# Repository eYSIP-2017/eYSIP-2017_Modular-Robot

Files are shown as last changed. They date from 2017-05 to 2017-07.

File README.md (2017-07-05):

# eYSIP-2017_Modular-Robot
A modular robot largely based of Alberto's [Dtto:Modular Robot](https://hackaday.io/project/9976-dtto-explorer-modular-robot), with modifications to expand its sensing and autonomous decision making capabilities. 
## Project Log
* ### Week 1: 23/05/2017 to 28/05/2017
     - Did some research on existing Modular Robots and planned our approach.
     - Added report on project approach. Resources can be found here: https://goo.gl/4ZXmfM
     - Tested the components given: Servo SG90, Bluetooth Module HC05, Arduino Nano, 1s 500mAh LiPos and Sharp IR GP2Y0A21.
     - Added Wiki page 'Testing the modules involved'
     - Started learning V-Rep and Lua scripting for simulating robot motions. 
* ### Week 2: 29/05/2017 to 4/06/2017
     - Tested the VL53L0X Lased Distance Measurement sensor, which offers precise distance measurement in a tiny package.
     - Learned Lua scripting for V-REP simulations and also practiced on the V-REP environment to learn basics of it.
     - Detected Wall/Obstacle using proximity sensor and restructured modules to cross it using 4 modules snake in V-REP.
     - Added Wiki page 'V-REP Simulations'
     - Edited CAD files of modules to increase hole diameter to 2mm due to screw unavailability
     - *NOTE: Module development delayed due to screw unavailability and also lately facing problems in 3D printer*
* ### Week 3: 05/06/2017 to 11/06/2017
     - Progress presentation 1 given on 06/06/2017.
     - Interfaced RF Module NRF24L01 and servo MG90S(for the hinges).
     - First Dtto V2 module build completed! Tested crawl motion with existing program.
     - 1.5x4mm screws found, decreased hole diameter for future modules.
     - Started writing program from scratch.
* ### Week 4: 12/06/2017 to 18/06/2017
     - Dtto modules 2 and 3 completed!
     - Interfaced the VL53L0X ToF sensor on one of the female faces.
     - Robot halts when it detects and obstacle and continues when obstacle is removed
     - Concluded that motor torque of MG90S is insufficient for most transformations.
* ### Week 5: 19/06/2017 to 25/06/2017   
     - Progress demonstration on 20/06/2017
     - Added Wiki page 'Building the modules', updated previous pages with more content.
     - Uploaded Arduino code with documentation
     - Edited CAD files and printed few parts for 'Mega Dtto', a scaled up version in order to support high torque servo GOTECK GS-5515MG
     - Started exploring methods to create a virtual Dtto environment for directly programming transformations, and also as a test bench.
* ### Week 6: 25/06/2017 to 02/07/2017 
     - Module 4 completed!
     - Implemented wheel motion using 4 modules.
     - Completed Virtual Dtto for setting angles, snake motion using Python remoteApi in V-REP.
     - Created poster for project exhibition.
     - Project Exhibition on 30/06/2017
* ### Week 7: 03/07/2017 to 05/07/2017 
     - Code updated and with better documentation.
     - Created Wiki page 'Wheel Motion: 4 modules' and 'Virtual Dtto'.
     - Created Final Report for project submission.
     - Did some basic testing for the Mega Dtto module.

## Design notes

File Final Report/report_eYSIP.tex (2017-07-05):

\documentclass[a4paper,12pt,oneside]{book}

%-------------------------------Start of the Preable------------------------------------------------
\usepackage[english]{babel}
\usepackage{blindtext}
%packagr for hyperlinks
\usepackage{hyperref}
\hypersetup{
    colorlinks=true,
    linkcolor=blue,
    filecolor=magenta,      
    urlcolor=cyan,
}

\urlstyle{same}
%use of package fancy header
\usepackage{fancyhdr}
\setlength\headheight{26pt}
\fancyhf{}
%\rhead{\includegraphics[width=1cm]{logo}}
\lhead{\rightmark}
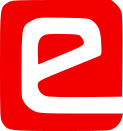
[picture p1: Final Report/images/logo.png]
\rhead{}
\fancyfoot[RE, RO]{\thepage}
\fancyfoot[CE, CO]{\href{http://www.e-yantra.org}{www.e-yantra.org}}

\pagestyle{fancy}

%use of package for section title formatting
\usepackage{titlesec}
\titleformat{\chapter}
  {\Large\bfseries} % format
  {}                % label
  {0pt}             % sep
  {\huge}           % before-code
 
%use of package tcolorbox for colorful textbox
\usepackage[most]{tcolorbox}
\tcbset{colback=cyan!5!white,colframe=cyan!75!black,halign title = flush center}

\newtcolorbox{mybox}[1]{colback=cyan!5!white,
colframe=cyan!75!black,fonttitle=\bfseries,
title=\textbf{\Large{#1}}}

%use of package marginnote for notes in margin
\usepackage{marginnote}

%use of packgage watermark for pages
%\usepackage{draftwatermark}
%\SetWatermarkText{\includegraphics{logo}}
\usepackage[scale=2,opacity=0.1,angle=0]{background}
\backgroundsetup{
contents={}
}

%use of newcommand for keywords color
\usepackage{xcolor}
\newcommand{\keyword}[1]{\textcolor{red}{\textbf{#1}}}

%package for inserting pictures
\usepackage{graphicx}
\graphicspath{ {images/} }

%package for highlighting
\usepackage{color,soul}

\usepackage{tikz}

\newcommand{\ExternalLink}{%
    \tikz[x=1.2ex, y=1.2ex, baseline=-0.05ex]{% 
        \begin{scope}[x=1ex, y=1ex]
            \clip (-0.1,-0.1) 
                --++ (-0, 1.2) 
                --++ (0.6, 0) 
                --++ (0, -0.6) 
                --++ (0.6, 0) 
                --++ (0, -1);
            \path[draw, 
                line width = 0.5, 
                rounded corners=0.5] 
                (0,0) rectangle (1,1);
        \end{scope}
        \path[draw, line width = 0.5] (0.5, 0.5) 
            -- (1, 1);
        \path[draw, line width = 0.5] (0.6, 1) 
            -- (1, 1) -- (1, 0.6);
        }
    }

%new command for table
\newcommand{\head}[1]{\textnormal{\textbf{#1}}}

%----------------------End of the Preamble---------------------------------------

\begin{document}

%---------------------Title Page------------------------------------------------
\begin{titlepage}
\raggedright
{\Large eYSIP 2017\\[1cm]}
{\Huge\scshape Modular Robot \\[.1in]}
\vfill
\begin{flushright}
{\large Srijal Poojari \\}
{\large Madhav Wagh \\}
{\large Mentors: Pushkar Raj, Aditya Panwar and Fayyaz Pocker \\}
{\large Duration of Internship: $ 22/05/2017-07/07/2017 $ \\}
\end{flushright}

{\itshape 2017, e-Yantra Publication}
\end{titlepage}
%-------------------------------------------------------------------------------

\chapter[Project Tag]{Modular Robot}
\section*{Abstract}
  This project is about homogeneous modular robotic modules, 
  which are coupled using mechanical and magnetic coupling. 
  The goal of the project is to explore existing modular robots, mainly the Dtto: Modular robot and expanding its capabilities. \\
  The modules are initially tested in a simulation environment for their feasibility (V-REP) and sensors (ToF) are interfaced to the modules for smart sensing and decision making. Snake motion, wheel motion, coupling/decoupling, obstacle detection and avoidance are achieved in practice. 

\subsection*{Completion status}
\textbf{Tasks given: }
\begin{enumerate}
\item Getting familiar with existing Models of Modular Robots\\ Status: Completed
\\ Details: Report has been earlier submitted on existing Modular Robots and project approach.

\item Interfacing Arduino ide with Servo, Bluetooth and Sensor 
\\ Status: Completed
\\ Details: Interfacing was completed with the following: Sharp IR 2Y0A21, Servo motors, Bluetooth module HC-05, nRF24L01 radio module and VL53L0X LASER ToF sensor.

\item Testing and selecting appropriate sensors to be added in the module.
\\ Status: Completed
\\ Details: Sensors were interfaced and the Vl53L0X was added to one of the modules.

\pagebreak

\item Making design changes in the modules for accommodating sensors. Adding more degree of freedom to the robot
\\ Status: Partially Completed
\\ Details: Design changes were done for the available screw sizes. Increasing degree of freedom of the robot was not achieved/supported by the Dtto v2 modules.

\item Assembling all the selected parts. Four robotic modules need to be produced.
\\ Status: Completed
\\ Details: Four robotic modules have been produced.

\item Applying algorithm to check different types of motion. Example: Wheel, Ladder, Snake.
\\ Status: Partially Completed
\\ Details: Wheel and Snake motion has been implemented. Servo motors are not powerful enough for Ladder maneuver.

\item Autonomous obstacle avoidance using sensor detection and self- reconfiguration.
\\ Status: Partially Completed
\\ Details: Obstacle detection has been achieved but self-reconfiguration is restricted by insufficient torque from servo motors.

\item Code and Documentation
\\ Status: Completed
\\ Details: The complete documentation and code can be found on our \href{https://github.com/eYSIP-2017/eYSIP-2017_Modular-Robot}{GitHub repository}.

\end{enumerate}

\noindent \textbf{Other work:}

\begin{enumerate}
\item V-REP simulations were performed while we were having problems finding the right screws and servo motors for the hinges.

\item A 'mega' Dtto module has been produced with larger size using the GO TECK GS-5515MG servo motors at the hinges

\item 'Virtual Dtto' environment has been created in V-REP using the python remoteApi for accepting commands via Bluetooth from the user which gets reflected on the simulated model. 

\end{enumerate}

\pagebreak

\section{Hardware parts}
\begin{itemize}
\item Primary:
      \begin{enumerate}
          \item Arduino Nano
          \\The brain of the Dtto. The main program runs on this and controls all others components in the Dtto.

          \item Bluetooth Module (HC-05)
          \\The HC-05 in the master module pairs up with the user's smartphone/tablet to accept commands from the user.

          \item RF Module (nRF24L01)
          \\The received commands by master is broadcasted to the slave modules (whenever required), which is the primary commands for slave modules

          \item Servo Motors (MG90S, SG90)
          \\Servo motors drive the module hinges and hooking mechanism. There are 5 servos used in total per module(2xMG90S-for the hinges and 3xSG90-for the hooks).

          \item VL53LOX LASER ToF Sensor 
          \\This is used to measure the distance from the module's base face (at the right moment) to detect obstacles present while the modules move.

      \end{enumerate}
      
\item Secondary:
      \begin{enumerate}
          \item Power: 2x 1s, 500mAh LiPos in series is given to the Arduino Nano at the Vin pin directly, and is regulated to 5.8V using an LM317 variable voltage regulator for the servos.

          \item Neodymium magnets: 4mm diameter, 3mm height(or 2x1.5mm stacked) are used for alignment of hooking mechanism when male and female faces are brought together. \\
          Amount required per module: 24/48 pieces for 3/1.5mm height

          \item Resistors (2.2k, 1.2k, 330), connecting wires, latching switch, prototype perf board, male and female headers, rubber bands.

      \end{enumerate}
\end{itemize}

\pagebreak

\section{Software used}
\begin{itemize}
\item Arduino IDE \\
Used to create and upload 'sketches' to the Arduino Nano. Also has a handy Serial Monitor for debugging.
\\Version used: 1.8.2
\\Download Link: \href{https://www.arduino.cc/en/main/software}{https://www.arduino.cc/en/main/software} 

\item Sloeber Eclipse IDE for Arduino\\
This is an alternative to the Arduino IDE which enables us to program the Arduino using the feature rich Eclipse IDE for C/C++. Most of out Dtto sketch was written on this.
\\Version used: 4.1 Beryllium
\\Download Link: \href{http://www.baeyens.it/eclipse/}{http://www.baeyens.it/eclipse/} 

\item Coppelia Robotics V-REP Simulator\\
V-REP was used for simulating the Dtto and also to create the Virtual Dtto environment.
\\Version used: 3.4.0
\\Download Link: \href{http://www.coppeliarobotics.com/downloads.html}{http://www.coppeliarobotics.com/downloads.html} 

\item Autodesk Fusion 360 \\
Used to modify the 3D CAD files of the modules before 3D printing them.
\\Version used: 2.0.3034
\\Download Link: \href{https://www.autodesk.com/products/fusion-360/students-teachers-educators}{https://www.autodesk.com/products/fusion-360/students-teachers-educators} 

\item Python 2.7\\
Python is necessary to run the Virtual Dtto as we are using the Python remoteApi for V-REP.
\\Version used: 2.7.13
\\Download Link: \href{https://www.python.org/downloads/release/python-2713/}{https://www.python.org/downloads/release/python-2713/} 

\item Fritzing\\
Fritzing was used to create all the schematics and interfacing diagrams.
\\Version used: 0.9.3b
\\Download Link: \href{http://fritzing.org/download/}{http://fritzing.org/download/}

\end{itemize}

\pagebreak

\section{Assembly of hardware}

\subsection{Circuit Diagram}
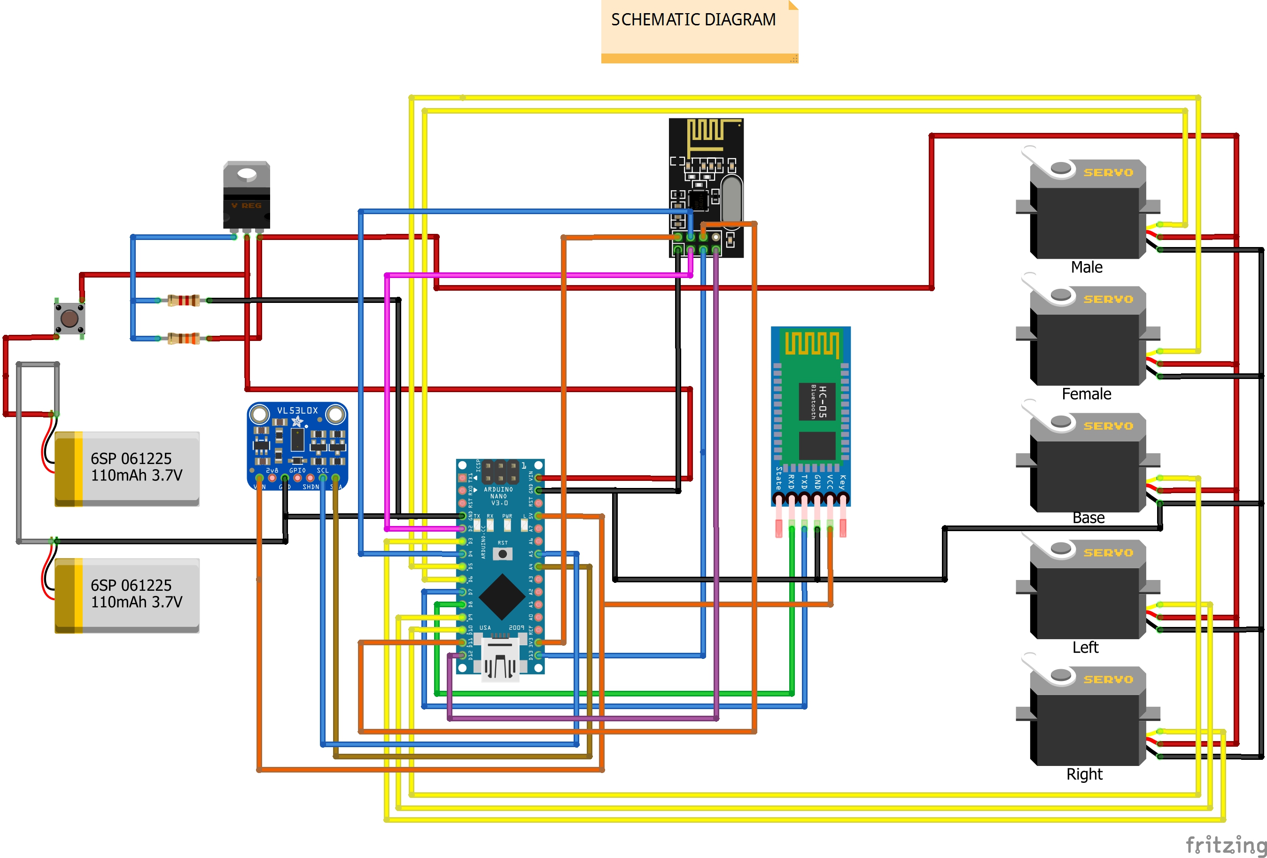
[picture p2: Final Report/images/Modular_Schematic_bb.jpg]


\subsection{Steps for assembly}
Steps for assembly can be found in this separate file \href{./Assembly steps for Dtto v2 Module.pdf}{here}.

\pagebreak

\section{Software and Code}

The program can be found in the eYSIP repository 
\href{https://github.com/eYSIP-2017/eYSIP-2017_Modular-Robot}{here}.\\

\noindent The entire program flow can be described by the flowcharts below:

\begin{itemize}

\item General flow \\
\begin{center}
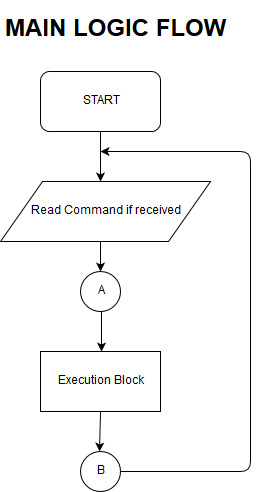
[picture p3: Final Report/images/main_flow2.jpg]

\end{center}

\end{itemize}
\pagebreak

\noindent The execution part can be elaborated further based on the type of command:

\begin{itemize}
\item Set angle \\

\vspace{-20pt}
\begin{center}
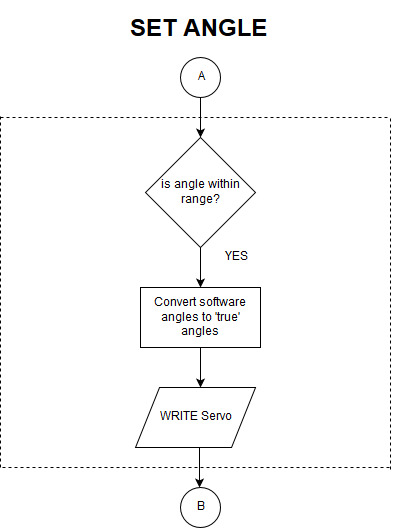
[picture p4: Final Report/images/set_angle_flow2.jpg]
 
\end{center}

\item Wheel \\
\vspace{-20pt}
\begin{center}
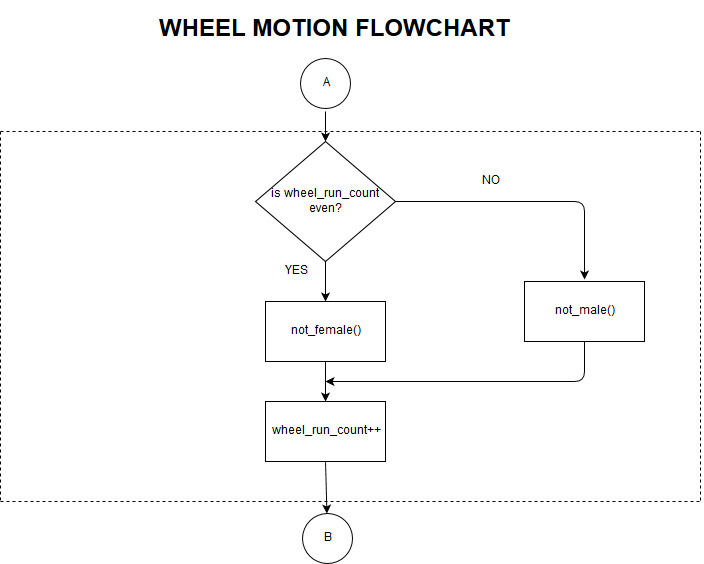
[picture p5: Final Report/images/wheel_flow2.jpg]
 
\end{center}

\item Snake \\
\begin{center}
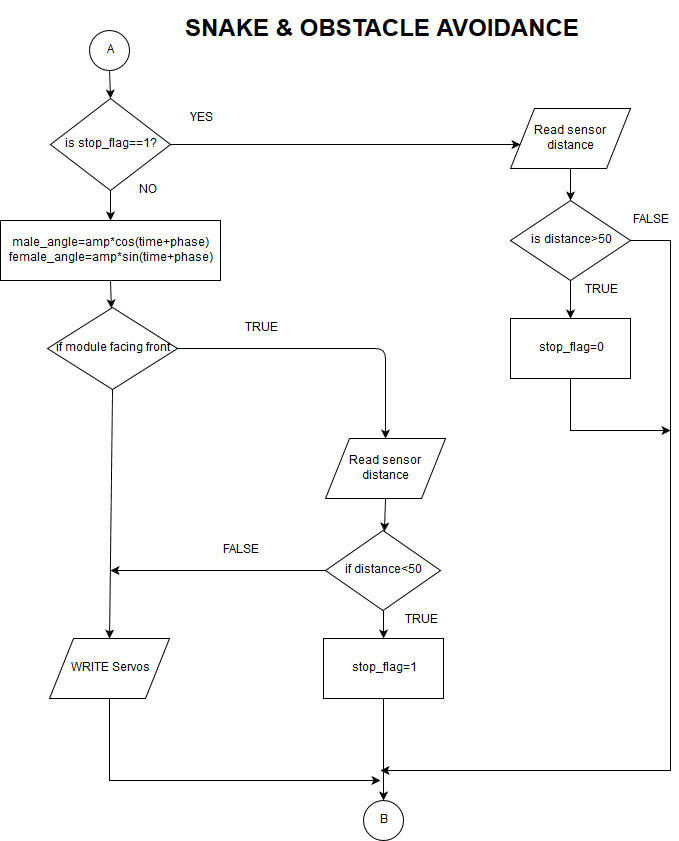
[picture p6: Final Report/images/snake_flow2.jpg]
 
\end{center}

\end{itemize}

\noindent Other than this, the entire code is well documented for detailed insights.

\pagebreak

\section{Use and Demo}
\subsection{Final Setup}
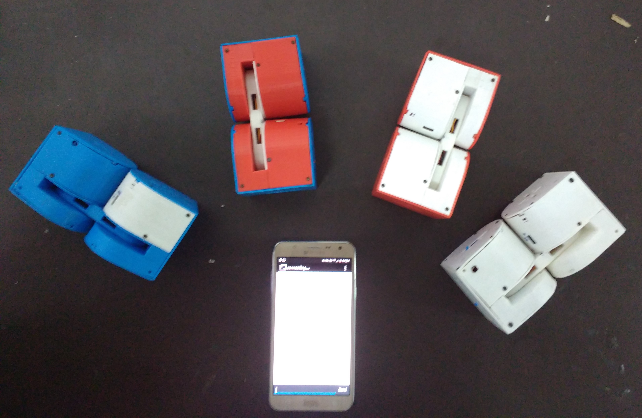
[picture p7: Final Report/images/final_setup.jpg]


\vspace{10pt}

\noindent The 4 Dtto modules assembled can be commanded using a Bluetooth device such as a smartphone shown above. The terminal application for Android devices can be downloaded \href{https://play.google.com/store/apps/details?id=Qwerty.BluetoothTerminal}{here}.

\subsection{User Instruction}
\noindent Load the Bluetooth Terminal application and connect to the master module from Options, Connect a device - Secure, 'Name of master HC-05'. Send the required commands. Best way to check all modules is by sending 'arm', which is to generate snake motion in all modules.

\vspace{10pt}

\noindent Structure of commands for controlling the Dtto using Bluetooth can be found in '\href{./Command_Definition.pdf}{Command\_Definitions.pdf}' present with this report or in our GitHub repository \href{https://github.com/eYSIP-2017/eYSIP-2017_Modular-Robot/blob/master/Final\%20Report/Command_Definition.pdf}{here}.

\subsection{Demonstration Video}
\begin{itemize}
\item \noindent Demonstration of snake motion and obstacle avoidance. \href{https://youtu.be/fWWrK-H1P5A}{\ExternalLink}

\item \noindent Demonstration of wheel motion. \href{https://youtu.be/WYdw9-lhOyw}{\ExternalLink}
\end{itemize}

\pagebreak

\section{Future Work}
There is vast amount of research and work which can be done
in the field of modular robotics and in our project, some 
enhancements which can be implemented in future are:

\begin{enumerate}
\item For faster processing and space saving, ESP8266/ESP32 can be used in place of Arduino Nano.

\item Using the basic modules implemented in the project with an overhead camera which can provide a reference frame for all modules.

\item Increasing the DOF of each module by adding rotating faces like the Dtto v3 which is under works.

\item Adding additional sensors for more feedback such as a  gravity sensor which can act as a reference for hinge angles.

\item Using a higher torque motor on the 'mega' modules being developed can add possibilities of different motions and transformations.
\end{enumerate}

\section{Bug report and Challenges}
\begin{itemize}
\item Appropriate screws (M1.7 x 4mm Flathead) were unavailable, so the CAD design was modified multiple times and the printing and assembly of modules was delayed.

\item The specified servo motor, MG92B is unavailable in local and online stores in India, so we're forced to use a lower torque motor MG90S, which is the closest that can be fit under the given module dimensions. Because of this many of the transformations was not possible.
\end{itemize}

\begin{thebibliography}{li}

\bibitem{dtto_alberto}
Alberto,
{\em Dtto - Explorer Modular Robot},
2016. \href{https://hackaday.io/project/9976-dtto-explorer-modular-robot}{\ExternalLink}

\bibitem{vrep_manual} 
V-REP User Manual. \href{http://www.coppeliarobotics.com/helpFiles/}{\ExternalLink}

\bibitem{hc05}
HC-05 specifications and AT commands. \href{https://www.itead.cc/wiki/Serial_Port_Bluetooth_Module_(Master/Slave)_:_HC-05}{\ExternalLink}

\bibitem{servo_cad}
Servo SG90, 3D CAD model. \href{https://grabcad.com/library/tower-pro-sg92r-servo-motor-1}{\ExternalLink}

\end{thebibliography}

\end{document}

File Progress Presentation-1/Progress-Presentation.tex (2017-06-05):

\documentclass[10pt, a4paper]{beamer}

\usetheme{Berkeley}
\usecolortheme{sidebartab}

\usepackage{graphicx}
\graphicspath{ {images/} }

\begin{document}
	\setbeamertemplate{sidebar left}{}
	\title{Progress Presentation-I}
	\subtitle{e-Yantra Summer Intership-2017 \\ Modular Robots}
	\author{Srijal Poojari\\Madhav Wagh\\
	\textbf{Mentors}: \\
	 Pushkar Raj, Aditya Panwar and Fayyaz Pocker}
	\institute{IIT, Bombay}
	\date{\today}
	%\addtobeamertemplate{sidebar left}{}{\includegraphics[scale = 0.3]{logowithtext.png}}
	\frame{\titlepage}

\setbeamertemplate{sidebar left}[sidebar theme]
\section{Overview of Project}
\begin{frame}{Overview of Project}
	\begin{itemize}
		\item \textbf{Project Name}:  Modular Robots
		\item \textbf{Objective} 
		\begin{enumerate}
		\item To build a Self-reconfigurable autonomous 	     		robot which can deliberately change shape by 				reorganizing connectivity between the modules.
		\linebreak
		\item To add sensors to the robot and make it smart. 		\\(To sense and take action according to the 				  environment)
		\linebreak
		\end{enumerate}
		\item \textbf{Deliverables}
		\begin{enumerate}
		 \item A stable modular robot which is able to 					  change its shape upon the need of the 					  environment.\linebreak
		\item Code and Documentation of each Task.
		\end{enumerate}
	\end{itemize}
\end{frame}

\section{Overview of Task}
\begin{frame}{Overview of Task}
	\begin{center}
    \begin{tabular}{ | l | p{6cm} | l |}
    \hline
     \textbf{Task No.} & \textbf{Task} & \textbf{Deadline}\\ \hline
     1 & Getting Familiar with existing models of Modular Robots & 2 days  \\ \hline
     
     2 & Interfacing Arduino IDE with Servo, Bluetooth and Sensor & 3 days  \\ \hline
     
     3 & Testing and selecting appropriate sensors to be added in the module & 2 days  \\ \hline
     
     4 & Make design changes in the modules for accommodating sensors.  & 4 days  \\ \hline
      
     5 & Assembling all the selected parts. Four robotic modules need to be produced & 4 days  \\ \hline
     
     6 & Applying algorithm to check different types of motion (Wheel, Snake, Ladder)  & 7 days  \\ \hline
     
     7 & Autonomous Obstacle Avoidance using sensor detection and self-reconfiguration & 6 days  \\ \hline
     
     8 & Code \& Documentation & 6 days  \\ \hline

    \end{tabular}
\end{center}
	
\end{frame}

\section{Tasks Accomplised}
\begin{frame}{Tasks Accomplised}
	\begin{itemize}
		\item \textbf{Task-1: Getting familiar with existing Modular Robots.}
		  \begin{itemize}
		  \item Collected information on existing modular robots.
		  \item Prepared a report and concluded that the Dtto Modular Robot is the most promising option under the given time and resources.
           \end{itemize}
           \vspace{15pt}
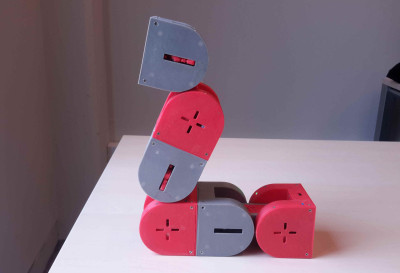
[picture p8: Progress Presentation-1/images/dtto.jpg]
        \centering   
		
	\end{itemize}
\end{frame}

\section{Tasks Accomplised}
\begin{frame}{Tasks Accomplised}
	\begin{itemize}
\item \textbf{Task-2 + 3: Selecting and interfacing sensors, servo motor and Bluetooth module with an Arduino.}
		\begin{itemize}
		  \item Successfully interfaced Bluetooth module HC-05 to HC-05 and HC-05 to PC/Android communication.
		  \item Interfaced servo motors and tested the Sharp IR sensor and VL53L0X ToF sensor for obstacle detection/distance measurement.
           \end{itemize}
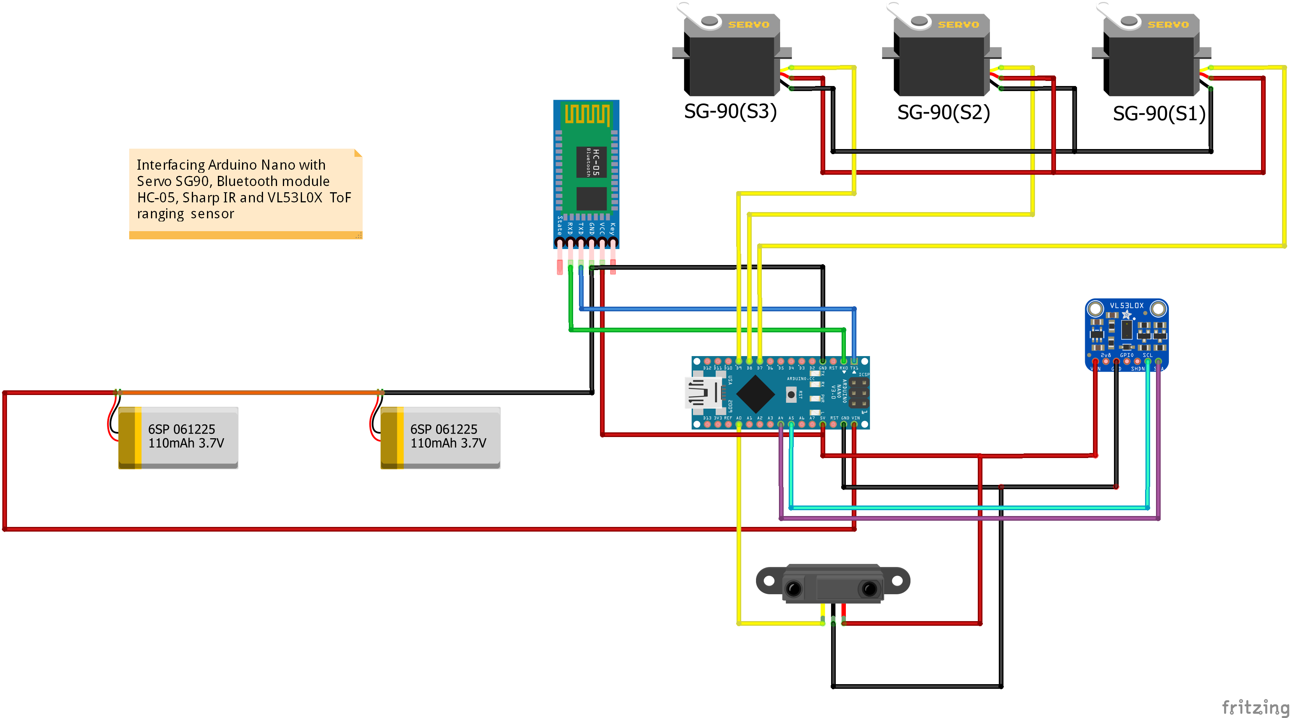
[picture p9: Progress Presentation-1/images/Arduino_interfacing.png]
           \centering
	\end{itemize}
\end{frame}

\section{Tasks Accomplised}
\begin{frame}{Tasks Accomplised}
	\begin{itemize}
		\item \textbf{Task-4: Making design changes in the modules.}
		\begin{itemize}
		    \item No major design changes were required as the modules have space for the tiny VL53L0X distance measurement sensor. 
		    \item Holes for the screws had to be expanded due to unavailability of M1.7x4mm screws.
		\end{itemize}
		\vspace{15pt}
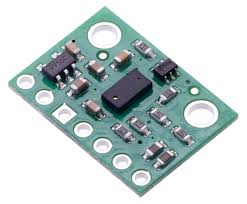
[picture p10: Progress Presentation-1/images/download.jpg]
        \centering
	\end{itemize}
\end{frame}

\section{Tasks Accomplised}
\begin{frame}{Tasks Accomplised}
	\begin{itemize}
		\item \textbf{Simulations in V-REP}
		    \begin{itemize}
		    \item Got familiar with the V-REP environment with Lua scripting and implemented practice simulations.
		    \item Understood existing Dtto movements and modified design to add proximity sensor which can detect obstacles and also measure its height.
		    \item Crossed the detected obstacles by reshaping modules in V-REP. \\ See video.
             \end{itemize}
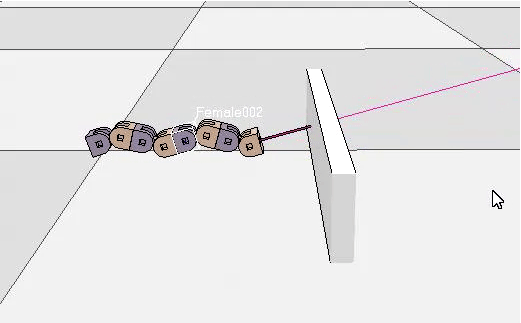
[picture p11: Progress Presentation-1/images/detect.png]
             \centering
	\end{itemize}
\end{frame}

\section{Tasks Accomplised}
\begin{frame}{Tasks Accomplised}
\begin{itemize}
		\item \textbf{Code and Documentation}
		    \begin{itemize}
		    \item Uploaded well-commented code (Arduino + Simulations) on GitHub for every stage.
		    \item Maintaining a detailed documentation of every step we take on GitHub Wiki of our repository.
            \end{itemize}
            
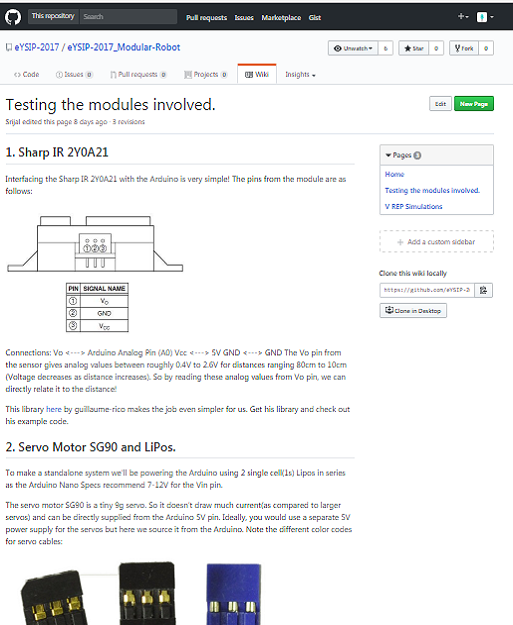
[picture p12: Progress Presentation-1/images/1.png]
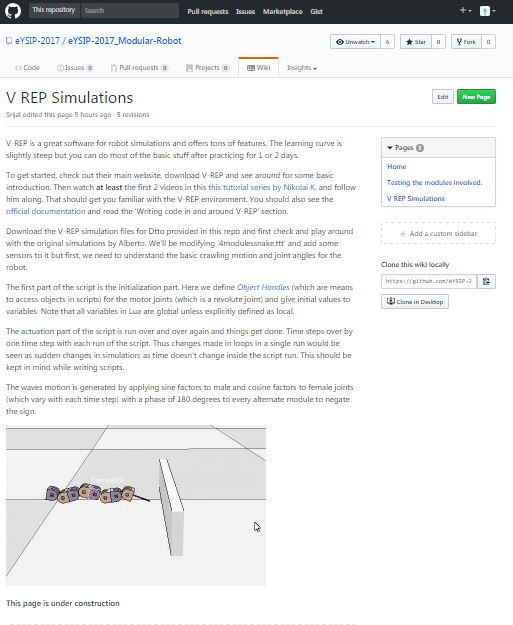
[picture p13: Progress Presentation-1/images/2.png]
        
            
\end{itemize}
\end{frame}		

\section{Challenges Faced}
\begin{frame}{Challenges Faced}
	\begin{itemize}
		\item Appropriate screws (M1.7x4mm Flathead) were unavailable, so the CAD design was modified multiple times and the printing and assembling of modules has been delayed. \linebreak
		\item The specified Servo motor, MG92B is unavailable in local and online stores so we're forced to use a lower torque motor MG90S, which is the closest that can be fit under the given module dimensions.
 
	\end{itemize}
\end{frame}

\section{Future Plans}
\begin{frame}{Future Plans}
	\begin{itemize}
		\item All printed parts assembled. Four Robotic modules to be assembled.
		
		\item Develop effective and generalized algorithms for different motions.
		
		\item  Obstacle detection using sensors and decision making to avoid/overcome the obstacle while robot moves from one point to another.

	\end{itemize}
\end{frame}

\section{Thank You}
\begin{frame}{Thank You}
	\centering\LARGE Thank You !
\end{frame}
\end{document}

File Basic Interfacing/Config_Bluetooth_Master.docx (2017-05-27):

STEPS TO CONFIGURE BLUETOOTH AS MASTER USING FTDI232

STEP-1) Interface the Bluetooth Module with the FT232 (USB to Serial Converter) as shown in Config_Bluetooth_ATComm.

STEP-2) Connect the FT232 to the USB Port of PC

After Connecting there will be a constant (POWER LED) on FT232 and a LED blinking quickly (twice in 1 second) on HC05.

STEP-3) If, FT232 driver software not installed, install it from (http://www.ftdichip.com/FTDrivers.htm)

STEP-4) Open the Serial Port on which FT232 driver is connected.

STEP-5) Master Configuration

1) Send AT Command. (Before Pressing Enter Press the Small button above EN Pin on HC05 (for AT Mode))

Get a Reply as OK

2) SEND AT+ROLE?

Will get a reply as 0 or 1, 0=> Slave, 1=> Master

3) SEND AT+ROLE=1 (Setting Module as Master)

4) SEND AT+NAME=MASTER-HC-05 (Renaming the Module)

5) SEND AT+NAME? (Checking Name of the Module)

6) SEND AT+CMODE=1 (Allows connecting to any address, Default CMODE is 0)

7) To bind another slave you need to bind with its MAC Address (48 bit address)

SEND AT+BIND= 0124, 71, CE187D

(Binding to the Slave module having MAC Address 01:24:71: CE: 18:7D)

8) SEND AT+BIND?

(Check all the Slave Bluetooth modules bound with the master)

Will return the MAC Address of modules which are bound

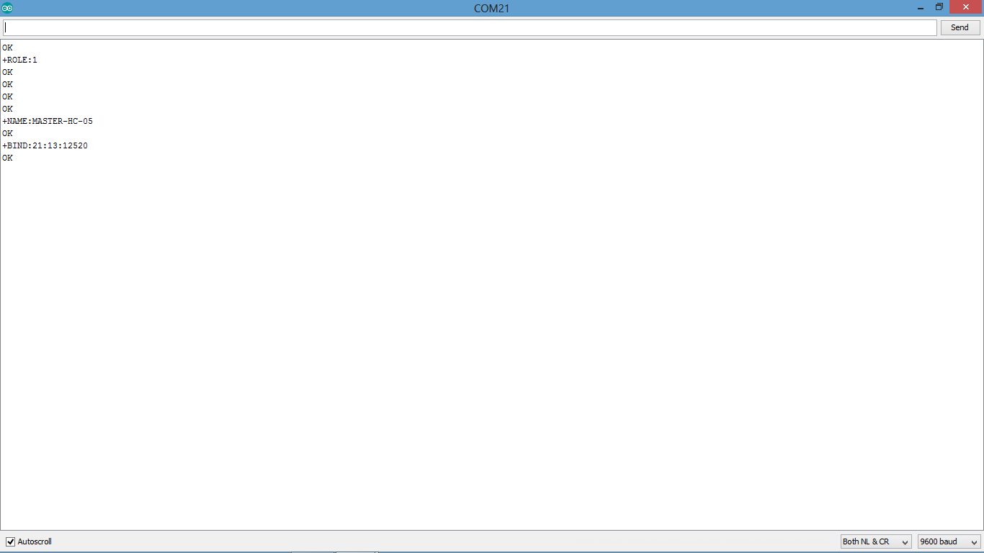
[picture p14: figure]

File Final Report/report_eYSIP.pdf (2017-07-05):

## eYSIP 2017

### Modular Robot

### Srijal Poojari Madhav Wagh Mentors: Pushkar Raj, Aditya Panwar and Fayyaz Pocker Duration of Internship: 22/05/2017 − 07/07/2017

2017, e-Yantra Publication

# Modular Robot

## Abstract

This project is about homogeneous modular robotic modules, which are coupled using mechanical and magnetic coupling. The goal of the project is to explore existing modular robots, mainly the Dtto: Modular robot and expanding its capabilities.
The modules are initially tested in a simulation environment for their feasibility (V-REP) and sensors (ToF) are interfaced to the modules for smart sensing and decision making. Snake motion, wheel motion, coupling/decoupling, obstacle detection and avoidance are achieved in practice.

### Completion status

Tasks given:

1. Getting familiar with existing Models of Modular Robots
Status: Completed
Details: Report has been earlier submitted on existing Modular Robots and project approach.
2. Interfacing Arduino ide with Servo, Bluetooth and Sensor
Status: Completed
Details: Interfacing was completed with the following: Sharp IR 2Y0A21, Servo motors, Bluetooth module HC-05, nRF24L01 radio module and VL53L0X LASER ToF sensor.
3. Testing and selecting appropriate sensors to be added in the module. Status: Completed
Details: Sensors were interfaced and the Vl53L0X was added to one of the modules.

1

4. Making design changes in the modules for accommodating sensors. Adding more degree of freedom to the robot
Status: Partially Completed
Details: Design changes were done for the available screw sizes. Increasing degree of freedom of the robot was not achieved/supported by the Dtto v2 modules.
5. Assembling all the selected parts. Four robotic modules need to be produced.
Status: Completed
Details: Four robotic modules have been produced.
6. Applying algorithm to check different types of motion. Example: Wheel, Ladder, Snake.
Status: Partially Completed
Details: Wheel and Snake motion has been implemented. Servo motors are not powerful enough for Ladder maneuver.
7. Autonomous obstacle avoidance using sensor detection and self- reconfiguration.
Status: Partially Completed
Details: Obstacle detection has been achieved but self-reconfiguration is restricted by insufficient torque from servo motors.
8. Code and Documentation
Status: Completed
Details: The complete documentation and code can be found on our GitHub repository. (https://github.com/eYSIP-2017/eYSIP-2017_Modular-Robot)

Other work:

1. V-REP simulations were performed while we were having problems finding the right screws and servo motors for the hinges.
2. A ’mega’ Dtto module has been produced with larger size using the GO TECK GS-5515MG servo motors at the hinges
3. ’Virtual Dtto’ environment has been created in V-REP using the python remoteApi for accepting commands via Bluetooth from the user which gets reflected on the simulated model.
www.e-yantra.org | 2

1.1. HARDWARE PARTS

## 1.1 Hardware parts

- Primary:
1. Arduino Nano
The brain of the Dtto. The main program runs on this and controls all others components in the Dtto.
2. Bluetooth Module (HC-05)
The HC-05 in the master module pairs up with the user’s smartphone/tablet to accept commands from the user.
3. RF Module (nRF24L01)
The received commands by master is broadcasted to the slave modules (whenever required), which is the primary commands for slave modules
4. Servo Motors (MG90S, SG90)
Servo motors drive the module hinges and hooking mechanism. There are 5 servos used in total per module(2xMG90S-for the hinges and 3xSG90-for the hooks).
5. VL53LOX LASER ToF Sensor
This is used to measure the distance from the module’s base face (at the right moment) to detect obstacles present while the modules move.
- Secondary:
1. Power: 2x 1s, 500mAh LiPos in series is given to the Arduino Nano at the Vin pin directly, and is regulated to 5.8V using an LM317 variable voltage regulator for the servos.
2. Neodymium magnets: 4mm diameter, 3mm height(or 2x1.5mm stacked) are used for alignment of hooking mechanism when male and female faces are brought together.
Amount required per module: 24/48 pieces for 3/1.5mm height
3. Resistors (2.2k, 1.2k, 330), connecting wires, latching switch, prototype perf board, male and female headers, rubber bands.
www.e-yantra.org | 3

1.2. SOFTWARE USED

## 1.2 Software used

- Arduino IDE
Used to create and upload ’sketches’ to the Arduino Nano. Also has a handy Serial Monitor for debugging.
Version used: 1.8.2
Download Link: https://www.arduino.cc/en/main/software
- Sloeber Eclipse IDE for Arduino
This is an alternative to the Arduino IDE which enables us to program the Arduino using the feature rich Eclipse IDE for C/C++. Most of out Dtto sketch was written on this.
Version used: 4.1 Beryllium
Download Link: http://www.baeyens.it/eclipse/
- Coppelia Robotics V-REP Simulator
V-REP was used for simulating the Dtto and also to create the Virtual Dtto environment.
Version used: 3.4.0
Download Link: http://www.coppeliarobotics.com/downloads.html
- Autodesk Fusion 360
Used to modify the 3D CAD files of the modules before 3D printing them.
Version used: 2.0.3034
Download Link: https://www.autodesk.com/products/fusion-360/studentsteachers-educators (https://www.autodesk.com/products/fusion-360/students-teachers-educators)
- Python 2.7
Python is necessary to run the Virtual Dtto as we are using the Python remoteApi for V-REP.
Version used: 2.7.13
Download Link: https://www.python.org/downloads/release/python-2713/ (https://www.python.org/downloads/release/python-2713/)
- Fritzing
Fritzing was used to create all the schematics and interfacing diagrams. Version used: 0.9.3b
Download Link: http://fritzing.org/download/
www.e-yantra.org | 4

1.3. ASSEMBLY OF HARDWARE

## 1.3 Assembly of hardware

### 1.3.1 Circuit Diagram

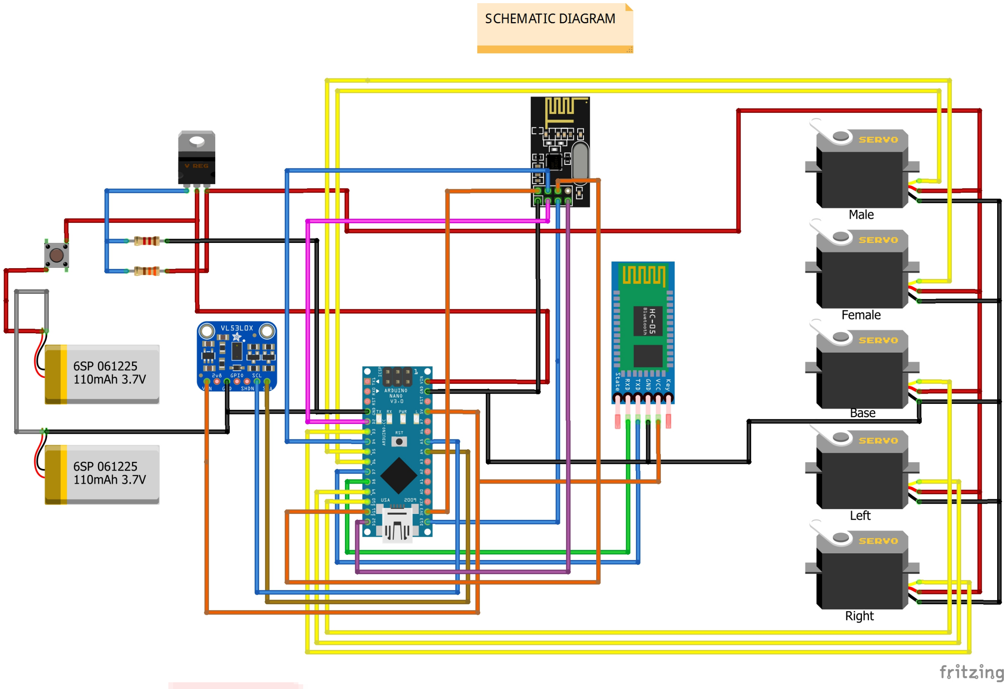
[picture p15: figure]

### 1.3.2 Steps for assembly

Steps for assembly can be found in this separate file here.

www.e-yantra.org | 5

1.4. SOFTWARE AND CODE

## 1.4 Software and Code

The program can be found in the eYSIP repository here. (https://github.com/eYSIP-2017/eYSIP-2017_Modular-Robot)

The entire program flow can be described by the flowcharts below:

- General flow

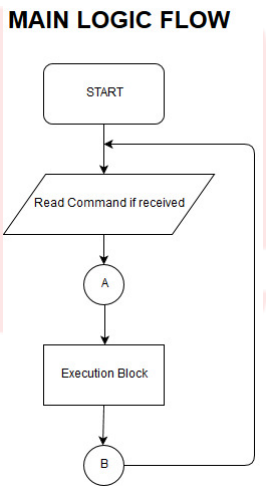
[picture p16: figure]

www.e-yantra.org | 6

1.4. SOFTWARE AND CODE

The execution part can be elaborated further based on the type of command:

- Set angle
- Wheel

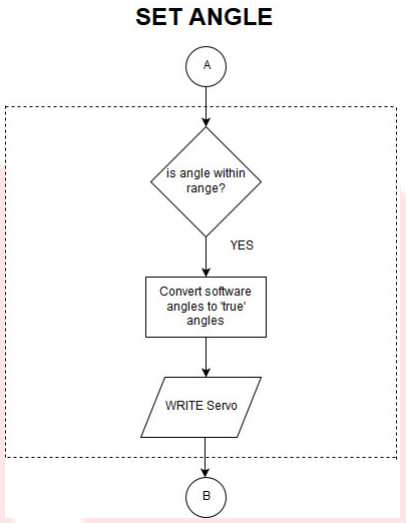
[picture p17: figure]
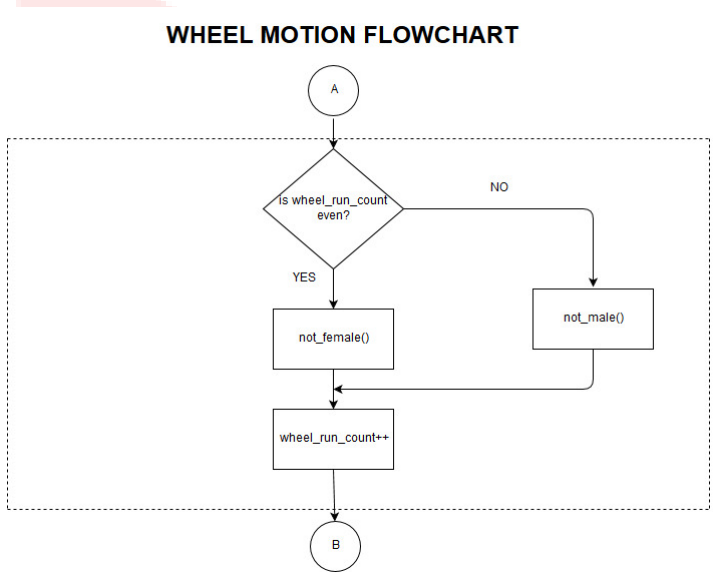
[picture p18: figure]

www.e-yantra.org | 7

1.4. SOFTWARE AND CODE
- Snake

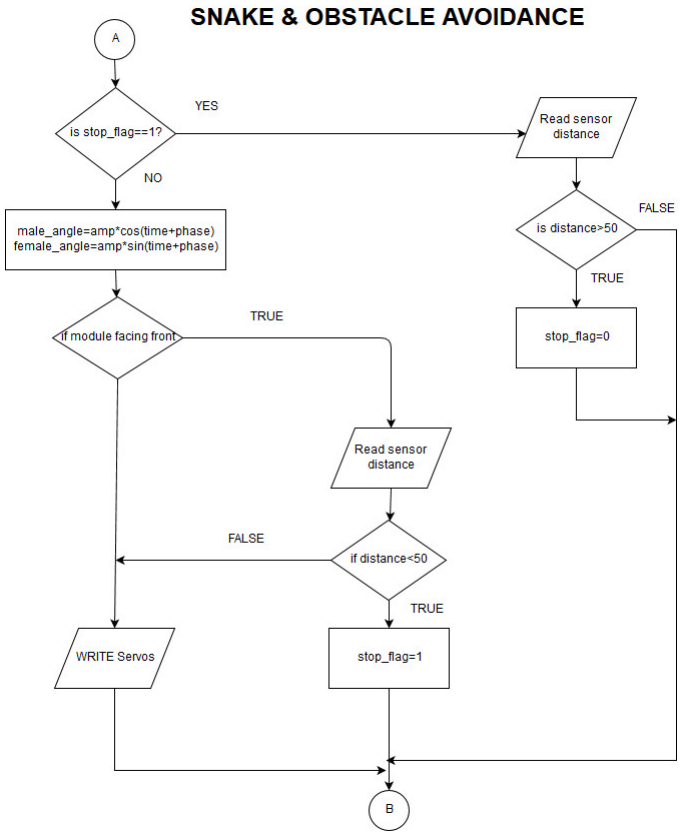
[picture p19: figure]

Other than this, the entire code is well documented for detailed insights.

www.e-yantra.org | 8

1.5. USE AND DEMO

## 1.5 Use and Demo

### 1.5.1 Final Setup

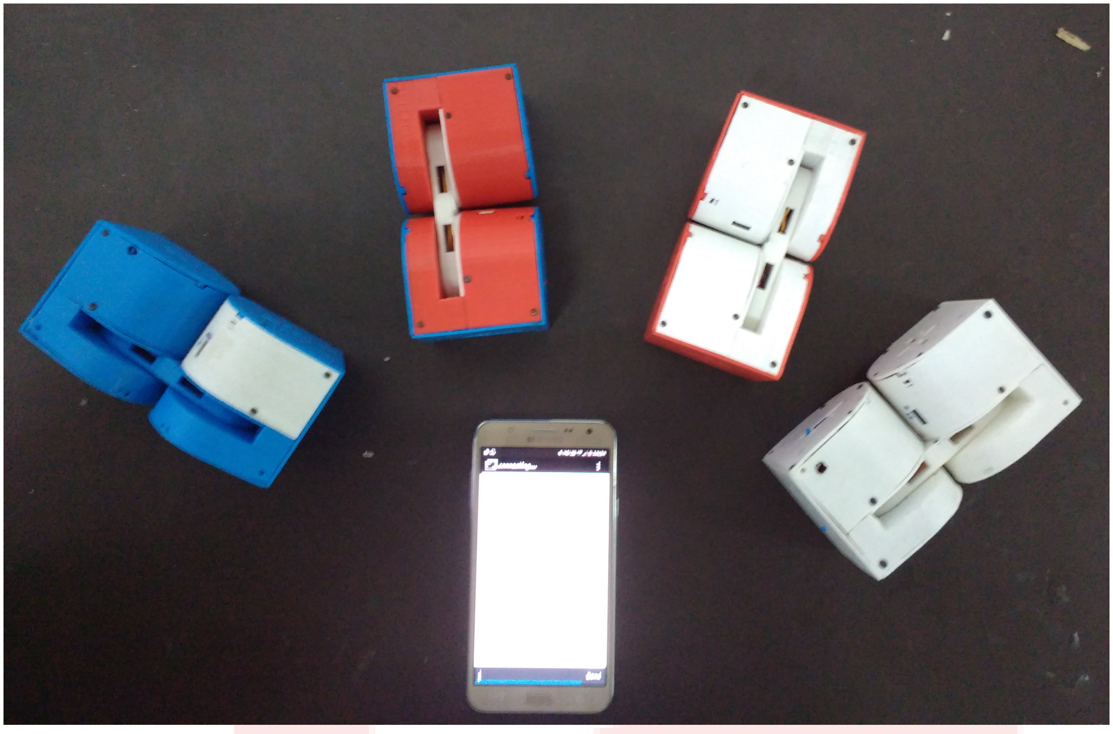
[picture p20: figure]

The 4 Dtto modules assembled can be commanded using a Bluetooth device such as a smartphone shown above. The terminal application for Android devices can be downloaded here. (https://play.google.com/store/apps/details?id=Qwerty.BluetoothTerminal)

### 1.5.2 User Instruction

Load the Bluetooth Terminal application and connect to the master module from Options, Connect a device - Secure, ’Name of master HC-05’. Send the required commands. Best way to check all modules is by sending ’arm’, which is to generate snake motion in all modules.

Structure of commands for controlling the Dtto using Bluetooth can be found in ’Command Definitions.pdf’ present with this report or in our GitHub repository here. (https://github.com/eYSIP-2017/eYSIP-2017_Modular-Robot/blob/master/Final%20Report/Command_Definition.pdf)

### 1.5.3 Demonstration Video

- Demonstration of snake motion and obstacle avoidance.
- Demonstration of wheel motion.
www.e-yantra.org | 9

1.6. FUTURE WORK

## 1.6 Future Work

There is vast amount of research and work which can be done in the field of modular robotics and in our project, some enhancements which can be implemented in future are:

1. For faster processing and space saving, ESP8266/ESP32 can be used in place of Arduino Nano.
2. Using the basic modules implemented in the project with an overhead camera which can provide a reference frame for all modules.
3. Increasing the DOF of each module by adding rotating faces like the Dtto v3 which is under works.
4. Adding additional sensors for more feedback such as a gravity sensor which can act as a reference for hinge angles.
5. Using a higher torque motor on the ’mega’ modules being developed can add possibilities of different motions and transformations.

## 1.7 Bug report and Challenges

- Appropriate screws (M1.7 x 4mm Flathead) were unavailable, so the CAD design was modified multiple times and the printing and assembly of modules was delayed.
- The specified servo motor, MG92B is unavailable in local and online stores in India, so we’re forced to use a lower torque motor MG90S, which is the closest that can be fit under the given module dimensions. Because of this many of the transformations was not possible.
www.e-yantra.org | 10

# Bibliography

[1] Alberto, Dtto - Explorer Modular Robot, 2016.
[2] V-REP User Manual.
[3] HC-05 specifications and AT commands.
[4] Servo SG90, 3D CAD model.

11

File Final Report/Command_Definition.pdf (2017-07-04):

COMMAND DESCRIPTION

Every command is sent via Bluetooth from PC/Mobile to the Master modules HC-05.

The master module receives the command and according to it takes specific action, it also broadcasts a relevant command set (if needed) to the slave modules for synchronization and movement.

Each command is a string of characters. Each character can be an alphabet or a number. Each character has some special meaning associated with it.

To know thoroughly about the commands go through the following sections of the code:

1) void listen_bluetooth() & void listen_RF()

These functions give an insight about the first character i.e. rf_rx_data[0]=bt_rx_data[0] which is received via wireless communication.

void listen_bluetooth() is called only if module is master. This receives data directly from user (PC/Mobile).

void listen_RF is called only if module is slave. Slave receives data from master module using RF(nRF24L01+) communication.

a => all modules ('a' means command for master as well as all slaves)

1 => command is for module number 1 (1 is always master)

n => command is for nth module

n=2,3,4,5….

2) void loop()

This function gives an insight about the second character i.e. final_rx_data[1] which is received via wireless communication.

r => snake | (run sinusoidal)
e => escape | (end all movements)
s => set_angle | (sets angle manually)
h => hook_attach | (attach modules=hook)
n => not angle | (switches angle between two states -90090)
w => wheel | (run wheel)

Further characters of the command, i.e. character number 3,4,5,6 and so on can be explained by looking at the individual functions called in the loop function, when a specific second character is switched by the switch case in the loop function.

I) snake (if second character is r)

Snake motion can be observed in male direction (direction where the male face is facing) or in the female direction. (Forward or reverse)

The 3

rd character defines the direction in case of snake motion.

m => male direction

f => female direction

Eg: arm, arf, 1rm, 1rf, 2rm, 2rf …

II) escape (if second character is e)

There is NO 3rd character for this command. The escape command for one specific or for all modules to stop is of 2 characters.

Eg: ae, 1e, 2e, 3e …

III) set_angle (if second character is s)

The 3

rd character defines the angle of which hinge servo (male/female) is to be set

m => male hinge servo

f => female hinge servo

The remaining characters(2 or 3) define the angle.

setting angle of hinge servos is accomplished by using the below commands

Eg: 1sm90, 1sf90, 1sm-90, 1sf-90 …

IV) hook_attach (if second character is h)

The 3

rd character defines the servo of which face is to be altered

b => base

l => left

r => right

The 4

th character defines the attaching/detaching

0 => detach

1 => attach

2 => detach and push (maximum detach)

setting angle of face servos (attaching/detaching) is accomplished using the below commands

Eg: ahb0,ahb1, 1hb0,1hb1 …

V) NOT angle (if second character is n)

'NOT' angle. Basically switches angle between 2 states, either 0<->90 or 0<->-90.

The 3

rd character defines the angle of which hinge servo (male/female) is to be not,

m => male hinge servo

f => female hinge servo

The remaining characters(2 or 3) define the angle.

Eg: anm90. 1nm-90, anf-90, 2nf-90 …

VI) wheel (if second character is w)

The 3

rd character defines either prepare or run

p=> prepare wheel

r=> run wheel

Eg: awp, awr

NOTE: All strings/words written in this document which are underlined and bold are COMMANDS except the note statement.

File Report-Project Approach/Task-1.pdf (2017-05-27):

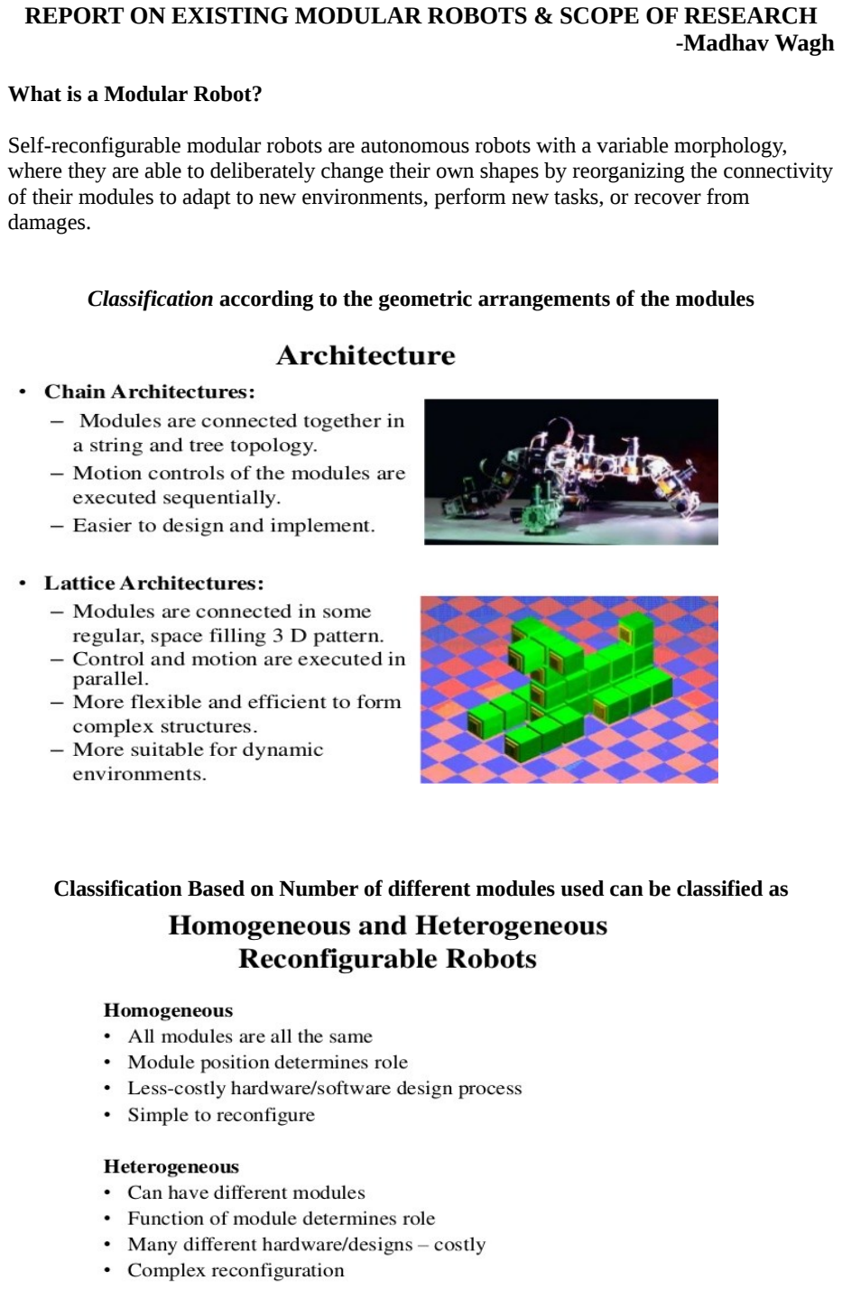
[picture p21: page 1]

REPORT ON EXISTING MODULAR ROBOTS & SCOPE OF RESEARCH -Madhav Wagh

What is a Modular Robot?

Self-reconfigurable modular robots are autonomous robots with a variable morphology, where they are able to deliberately change their own shapes by reorganizing the connectivity of their modules to adapt to new environments, perform new tasks, or recover from damages.

Classification according to the geometric arrangements of the modules

Classification Based on Number of different modules used can be classified as

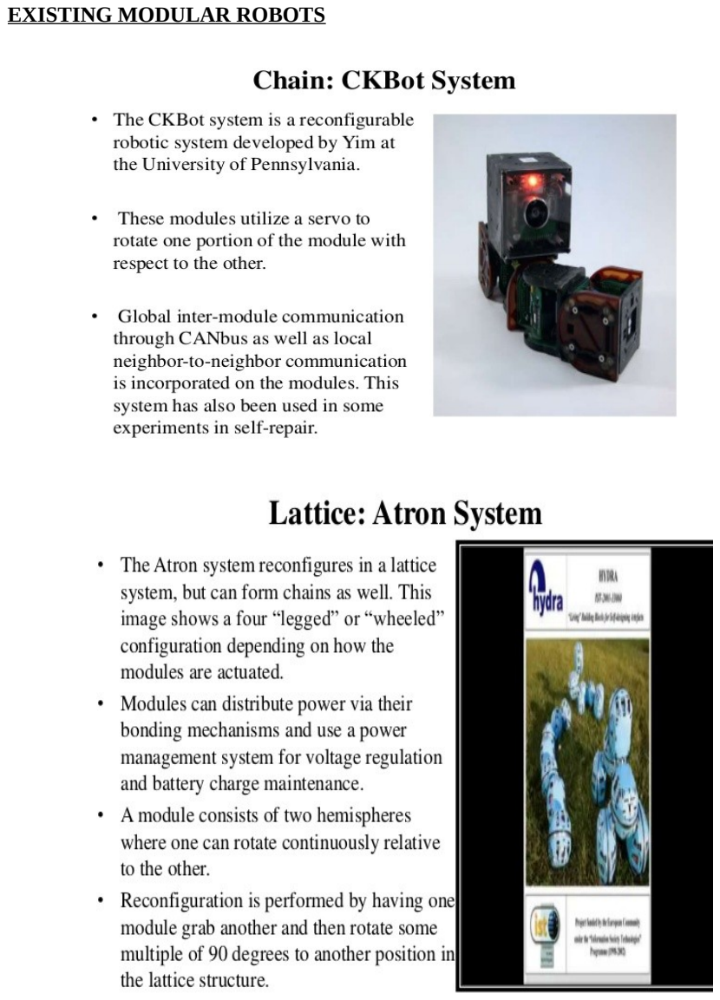
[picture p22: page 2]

EXISTING MODULAR ROBOTS

2D Modular Robots | Homogeneity/ Heterogeneity | Dynamic Motion | Comments
CEBOT (Nagoya Univ.) | Hetero | No | A modular robot proposed first
Fractum (AIST) | Homo | No | First exmeriment of self-repair
Mirco-module (AIST) | Homo | No | Micro-sizing into 2cm cube using SMA
Metamorphic Robot (Johns Hopkins Univ.) | Homo | No | Hexagonal link mechanism
Modular robot of Riken | Homo | No | Cube-shape, can be stuck vertically
3D Modular Robots | Homogeneity / Heterogeneit y | Dynamic Motion | Self-reconfigurab lity | Control System | Comments
3D Self-reconfigurabl e Structure (AIST) | Homo | No | Yes | Centralized | First 3D self-reconfigurabl e homogeneous modular structure
Crystaline (Dartmouth) | Homo | No | Yes | Centralized | Shrinkable module to build 2D and 3D structures
Moledule (Dartmouth) | Homo | No | Yes | Centralized | Composed of a link and two connecting parts
I-Cube (CMU) | Hetero | No | Yes | Centralized | Consists of two types of modules, links and cube. The link is actuated
CONRO (USC) | Homo | Yes | Yes | Centralized | Serially connected modules with small degrees

| | | | | of freedom for dynamic motion
Polybot (Xerox PARC) | Homo | Yes | Yes | Centralized | Serially connected modules with small degrees of freedom for dynamic motion
3D Modular Structure (TiTech) | Homo | No | Yes | Centralized | Reconfigurati on performed by pneumatic actuator
RBR (TiTech) | Hetero | Yes | Yes | Centralized | Reconfigurabl e robotic arm for space applications
"Modular Transformer" MTRAN (AIST) | Homo | Yes | Yes | Centralized | Succeeded in moving by changing its locomotion mode using 9 modules
SkyWalker (CMU) | Hetero | Yes | No | Centralized | An example of modular space robot
Tetrobot (Renssaeler Polytech. Inst.) | Hetero | Yes | No | Centralized | An example of a modular robot with many possible configuration s

CONCLUSION

After going through various modular robots(mentioned in the table),

The Scope for Research are:
- There is a need for interfacing of Sensors to Modular Robots.
- Programming them with Sensor Feedback.
-Making them interactive with the environment.

This can be efficiently, timely and proficiently done using Dtto Modular Robot because,
1) It has already provided free space for Sensor Attachment
2) Design and code is open source (for initial reference)
3) It is inspired from MTRAN
4) IR, Proximity, Gyro Sensors can be easily attached to each module
5) Modules are homogeneous
6) Thus program one program all

REFERENCES

1) http://thesis.library.caltech.edu/4189/1/Chen_im_1994.pdf
2) http://155.69.254.10/users/risc/Pub/Conf/98-c-icarcv-semors.pdf
3) https://staff.aist.go.jp/e.yoshida/test/research-e.htm
4) https://hackaday.io/project/9976-dtto-explorer-modular-robot

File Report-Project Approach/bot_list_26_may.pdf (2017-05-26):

### Polypod, 1993:

Made up of 2 types of modules, segment and node. Each segment module contains all the components to be a stand-alone robot in itself (except for power): •Computation: Motorola XC68HC11E2 (generously donated by Motorola) •Actuation: Two small DC motors with lead screw transmission
•Sensing:
•IR proximity sensing
•crude force/torque sensing using IR

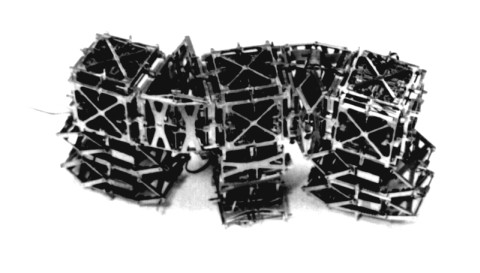
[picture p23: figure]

•joint angle position sensing (potentiometers)
•Inter-module Communication: Global synchronous communication (Motorola SPI with RS485 drivers) between 68HC11's plus local IR communication between adjacent modules.
Nodes are rigid cube shaped modules roughly 2"x2"x2" with 6 connection ports whose main purpose is to hold gel-cel batteries and to allow for non-serial chain robots.
Ref: http://robotics.stanford.edu/users/mark/polypod.html

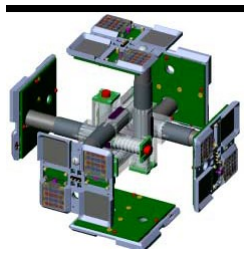
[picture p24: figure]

Telecubes, 1998:
All the six faces of the cubical module are attached to the core using linear actuators. They have IR sensors on their faces to detect other modules and attach magnetically to other modules.

Refer ‘telecubes.pdf’


### PolyBot G3, 2002:

These have electrical contacts to transmit data and power, IR sensors to detect and orient with other modules and attach using Shape Memory Alloy latches. A flat brushless motor is used at the hinges with precise angle detection (0.04 degrees) using hall effect sensors

Refer ‘Evolution_of_PolyBot.pdf’ and this. (http://archive.li/ErqNo)


### ATRON, 2003:

Each module consists of 2 half spheres which can independently rotate about themselves. Modules have metallic hooks and attachment bars. Hooks are actuated and is used to combine with other modules. Detailed design is explained in “ATRON_Design.pdf”

Also see: https://www.youtube.com/watch?v=SYizuooEs7s (https://www.youtube.com/watch?v=SYizuooEs7s)

### Molecubes, 2005:

This has a unique design where the cube has 2 halves which diagonally swivel about each other. They attach/ detach by selectively weakening electromagnets. Each module has a microcontroller which decides motion based on time and contact events. Data and power is transmitter through the metal contacts.

Reference, (http://www.news.cornell.edu/stories/2005/05/researchers-build-robot-can-reproduce) Video. (https://www.youtube.com/watch?v=gZwTcLeelAY)


### Miche, 2006:


This system uses self-disassembly over self-assembly which is seen in other examples.
The cubes are assembled manually into a larger cube and the attach with each other using electromagnets. The modules are autonomous detect the presence of its immediate neighbor using infrared sensors. They collectively decide who should and should not be in the final structure-to-be-formed and let go and drop off under an external force, in this case, gravity.

Refer ‘Miche.pdf’


### Roombots, 2009:

It has diagonally swiveling half cube structure like the molecubes, but these cubes have a hook based attaching system like the M-TRAN. Modules are big so can support lots of sensors.

Video (https://www.youtube.com/watch?v=0XDpT8hI89k)

### CKBot, 2009:


CKBot modules could either be assembled manually or they can self-reconfigure using magnets on their faces which were strong enough to hold 7 modules vertically before it caused chain disconnection. Modules can be connected manually using 3M screws and can be connected electrically to share power and communication on a CAN (Controller Area Network) bus using a 20 pin header. Modules that are on the same bus can communicate amongst each other using infra red (IR). There are seven IR pairs on a module that act as transmitters and receivers. Bluetooth and Xbee modules are used to connect via wireless and translates messages to and from the CANbus. Reference: http://www.modlabupenn.org/2009/09/24/ckbot/


### SMORES, 2012:

Each modules has an ARM Cortex M3 based core with
3 dual motor drivers driving 5 motors(4 for motion, 1 for interlocking modules). Modules communicate with each other using Xbee.

Refer ‘SMORES.pdf’ and this. (http://modlabupenn.org/smores/)

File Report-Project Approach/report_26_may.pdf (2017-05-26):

Report on Existing Modular Robots and Approach on Increasing its Functionality May 26, 2017

Based on the existing models of a Modular Robot or similar projects, we get to see a wide variety of methods used for control, data/power transmission, actuation, sensing.

All these methods have their own limitations and our modular robot would be primarily focusing on a low-cost, maximum capability (in terms of ability to sense the surroundings and moving from one place to another) approach.

The Dtto Modular Robot is the most promising option under the given time and resources as the body is 3D printed and system based on Arduino which is relatively easy to develop. To expand its capabilities, a number of things could be done:
- IR obstacle detection on all flat faces of the module. If this is done, it will help detect obstacles in any configuration and make decisions to avoid the obstacle.
- Add IR receivers on faces which can detect the IR sent from faces and locate other modules. Each face will transmit different IR codes so the receiving module will have some idea about its orientation
- Ultrasonic sensors could also be used for better immunity to lighting changes but they are bulkier than IR sensors. There are modules such as the MaxSonar EZ1, (https://www.sparkfun.com/products/639) which are smaller than usual but still a bit bulky(roughly 2x2x1.5cm).
- Gyroscope to sense direction of gravity would help in making motion decisions.
- A camera module could be developed based of tiny FPV cameras used in RC Planes and drones. The sent video could be processed in a computer and used to send feedback to the Modules.
- Using a standalone MCU like the ESP32 which has built in WiFi+BLE would save lots of space and make room for more sensors.

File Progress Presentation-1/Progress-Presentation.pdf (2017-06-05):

Progress Presentation-I; e-Yantra Summer Intership-2017 Modular Robots; Srijal Poojari Madhav Wagh Mentors:; IIT, Bombay; June 5, 2017

# Pushkar Raj, Aditya Panwar and Fayyaz Pocker

Overview of Project; Overview of Task; Tasks Accomplised; Challenges Faced; Future Plans; Thank You; Project Name: Modular Robots; Objective; the modules.; Deliverables; the need of the environment.; Code and Documentation of each Task.

Progress Presentation-I Srijal Poojari Madhav Wagh Mentors: Pushkar Raj, Aditya Panwar and Fayyaz Pocker

1 | To build a Self-reconfigurable autonomous robot which can deliberately change shape by reorganizing connectivity between
2 | To add sensors to the robot and make it smart. (To sense and take action according to the environment)
1 | A stable modular robot which is able to change its shape upon

Progress
Presentation-I

Srijal Poojari
Madhav Wagh
Mentors:
Pushkar Raj,
Aditya Panwar
and Fayyaz
Pocker

Overview of
Project

Overview of Task

Tasks
Accomplised

Tasks
Accomplised

Tasks
Accomplised

Tasks
Accomplised

Tasks
Accomplised

Challenges Faced

Future Plans

# Overview of Task

Task No. | Task | Deadline
1 | Getting Familiar with existing models of Modular Robots | 2 days
2 | Interfacing Arduino IDE with Servo, Blue-tooth and Sensor | 3 days
3 | Testing and selecting appropriate sensors to be added in the module | 2 days
4 | Make design changes in the modules for accommodating sensors. | 4 days
5 | Assembling all the selected parts. Four robotic modules need to be produced | 4 days
6 | Applying algorithm to check different types of motion (Wheel, Snake, Ladder) | 7 days
7 | Autonomous Obstacle Avoidance using sensor detection and self-reconfiguration | 6 days
8 | Code & Documentation | 6 days

Progress Presentation-I; Srijal Poojari Madhav Wagh Mentors: Pushkar Raj, Aditya Panwar and Fayyaz Pocker; Overview of Project; Overview of Task; Tasks Accomplised; Challenges Faced; Future Plans

Task-1: Getting familiar with existing Modular Robots. Collected information on existing modular robots.

# Prepared a report and concluded that the Dtto Modular Robot is

the most promising option under the given time and resources.

Progress Presentation-I; Srijal Poojari Madhav Wagh Mentors: Pushkar Raj, Aditya Panwar and Fayyaz Pocker; Overview of Project; Overview of Task; Tasks Accomplised; Challenges Faced; Future Plans; and Bluetooth module with an Arduino.; HC-05 to PC/Android communication.; measurement.

# Task-2 + 3: Selecting and interfacing sensors, servo motor

# Successfully interfaced Bluetooth module HC-05 to HC-05 and

# Interfaced servo motors and tested the Sharp IR sensor and VL53L0X ToF sensor for obstacle detection/distance

Progress Presentation-I; Srijal Poojari Madhav Wagh Mentors: Pushkar Raj, Aditya Panwar and Fayyaz Pocker; Overview of Project; Overview of Task; Tasks Accomplised; Challenges Faced; Future Plans; M1.7x4mm screws.

Task-4: Making design changes in the modules.

# No major design changes were required as the modules have

space for the tiny VL53L0X distance measurement sensor.

# Holes for the screws had to be expanded due to unavailability of

Progress Presentation-I; Srijal Poojari Madhav Wagh Mentors: Pushkar Raj, Aditya Panwar and Fayyaz Pocker; Overview of Project; Overview of Task; Tasks Accomplised; Challenges Faced; Future Plans; Simulations in V-REP; implemented practice simulations.; measure its height.; See video.

# Got familiar with the V-REP environment with Lua scripting and

# Understood existing Dtto movements and modified design to add proximity sensor which can detect obstacles and also

Crossed the detected obstacles by reshaping modules in V-REP.

Progress Presentation-I; Srijal Poojari Madhav Wagh Mentors: Pushkar Raj, Aditya Panwar and Fayyaz Pocker; Overview of Project; Overview of Task; Tasks Accomplised; Challenges Faced; Future Plans; Code and Documentation; GitHub for every stage.; GitHub Wiki of our repository.

# Uploaded well-commented code (Arduino + Simulations) on

# Maintaining a detailed documentation of every step we take on

Progress Presentation-I; Srijal Poojari Madhav Wagh Mentors: Pushkar Raj, Aditya Panwar and Fayyaz Pocker; Overview of Project; Overview of Task; Tasks Accomplised; Challenges Faced; Future Plans; module dimensions.

# Appropriate screws (M1.7x4mm Flathead) were unavailable, so the CAD design was modified multiple times and the printing

and assembling of modules has been delayed.

# The specified Servo motor, MG92B is unavailable in local and online stores so we’re forced to use a lower torque motor MG90S, which is the closest that can be fit under the given

Progress Presentation-I; Srijal Poojari Madhav Wagh Mentors: Pushkar Raj, Aditya Panwar and Fayyaz Pocker; Overview of Project; Overview of Task; Tasks Accomplised; Challenges Faced; Future Plans; assembled.; motions.; to another.

# All printed parts assembled. Four Robotic modules to be

# Develop effective and generalized algorithms for different

# Obstacle detection using sensors and decision making to avoid/overcome the obstacle while robot moves from one point

Progress Presentation-I; Srijal Poojari Madhav Wagh Mentors: Pushkar Raj, Aditya Panwar and Fayyaz Pocker; Overview of Project; Overview of Task; Tasks Accomplised; Challenges Faced; Future Plans; Thank You; Thank You !

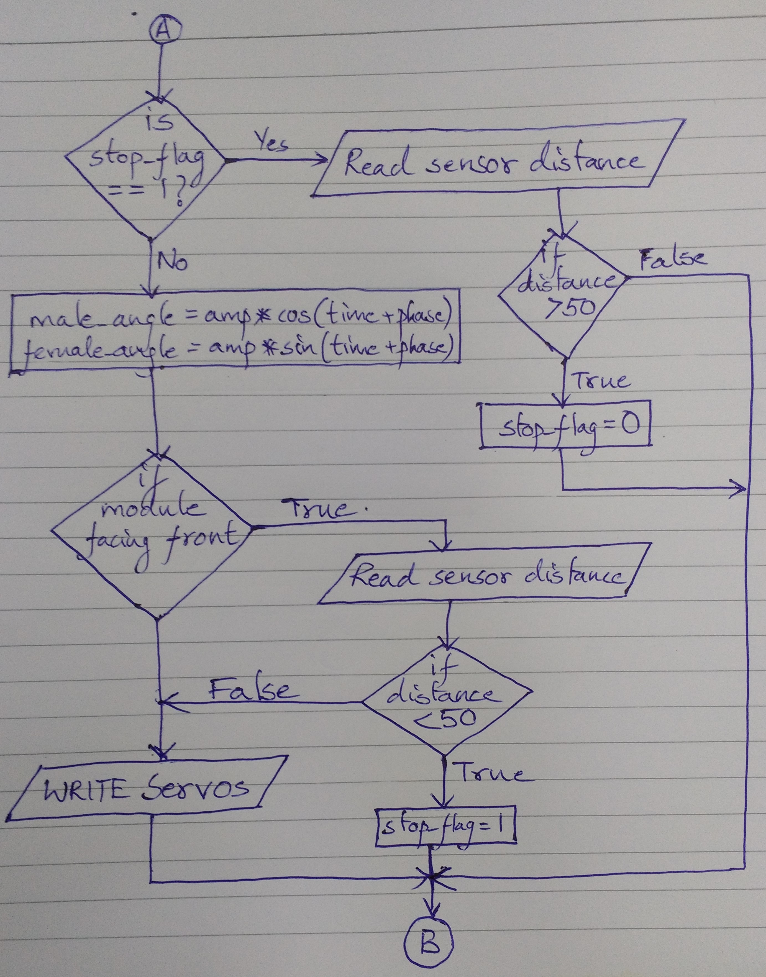
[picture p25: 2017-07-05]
Final Report/images/snake_flow.jpg

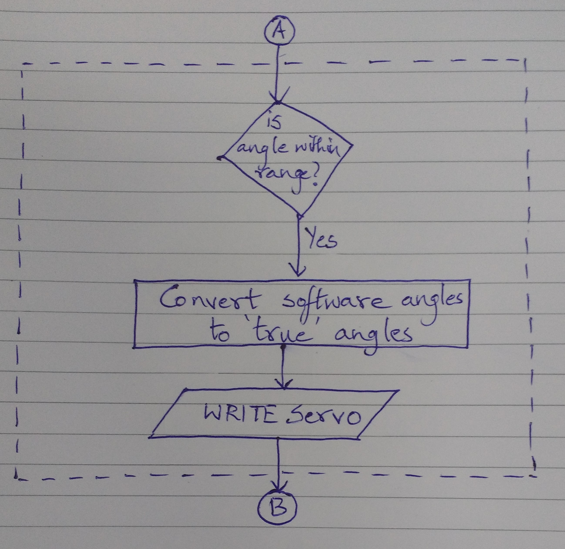
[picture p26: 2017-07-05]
Final Report/images/set_angle_flow.jpg

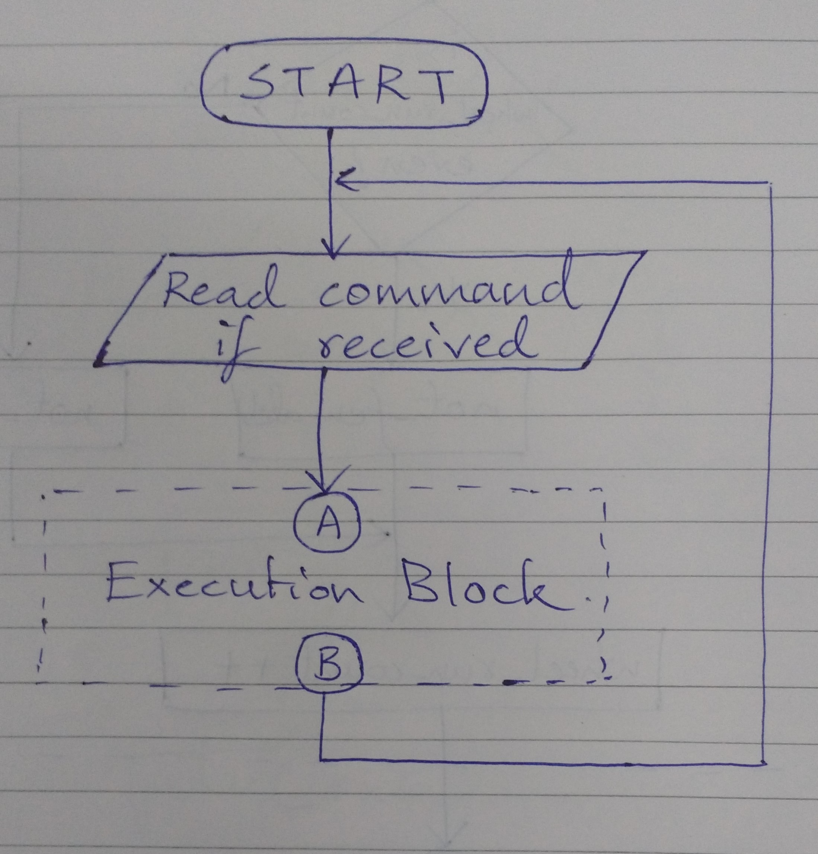
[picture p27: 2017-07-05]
Final Report/images/main_flow.jpg

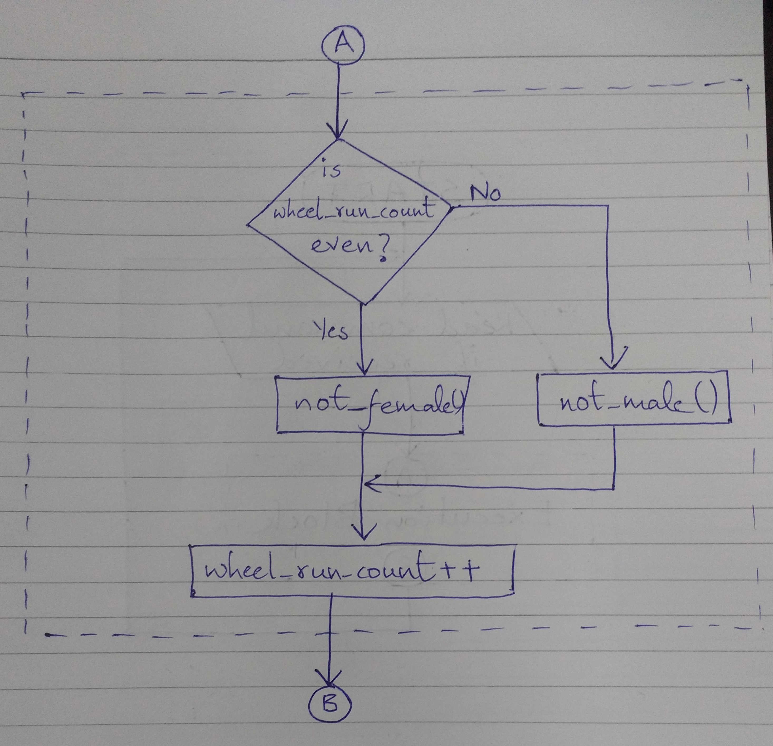
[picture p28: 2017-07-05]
Final Report/images/wheel_flow.jpg

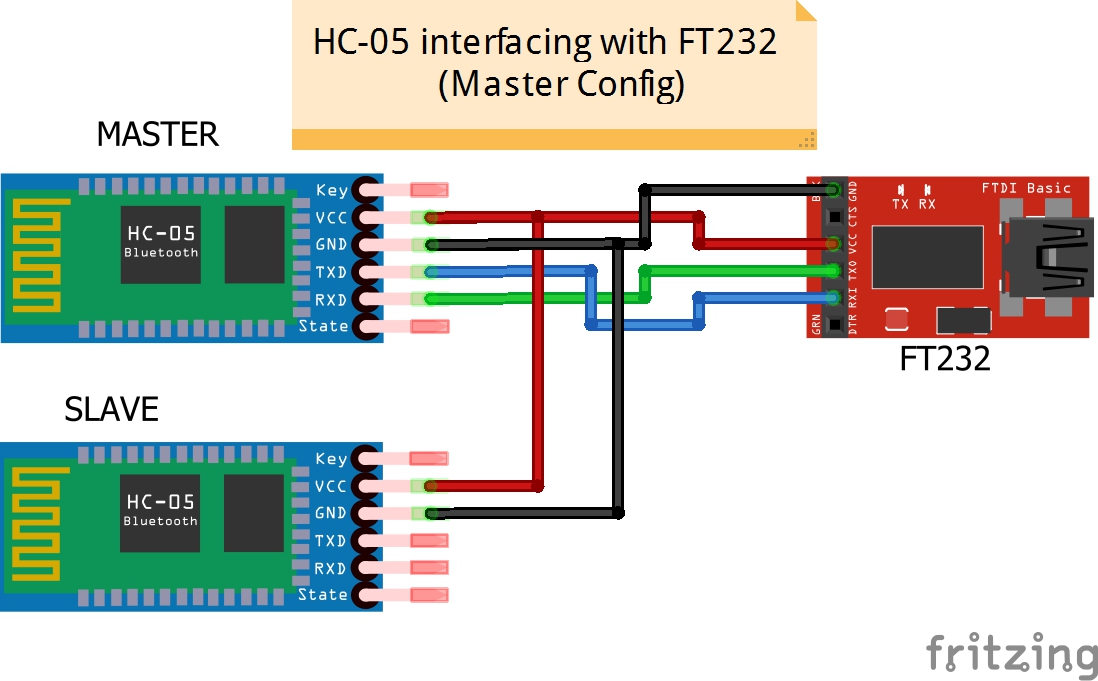
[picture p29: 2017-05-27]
Basic Interfacing/Schematics/Config_Bluetooth_ATComm(Master Config).jpg

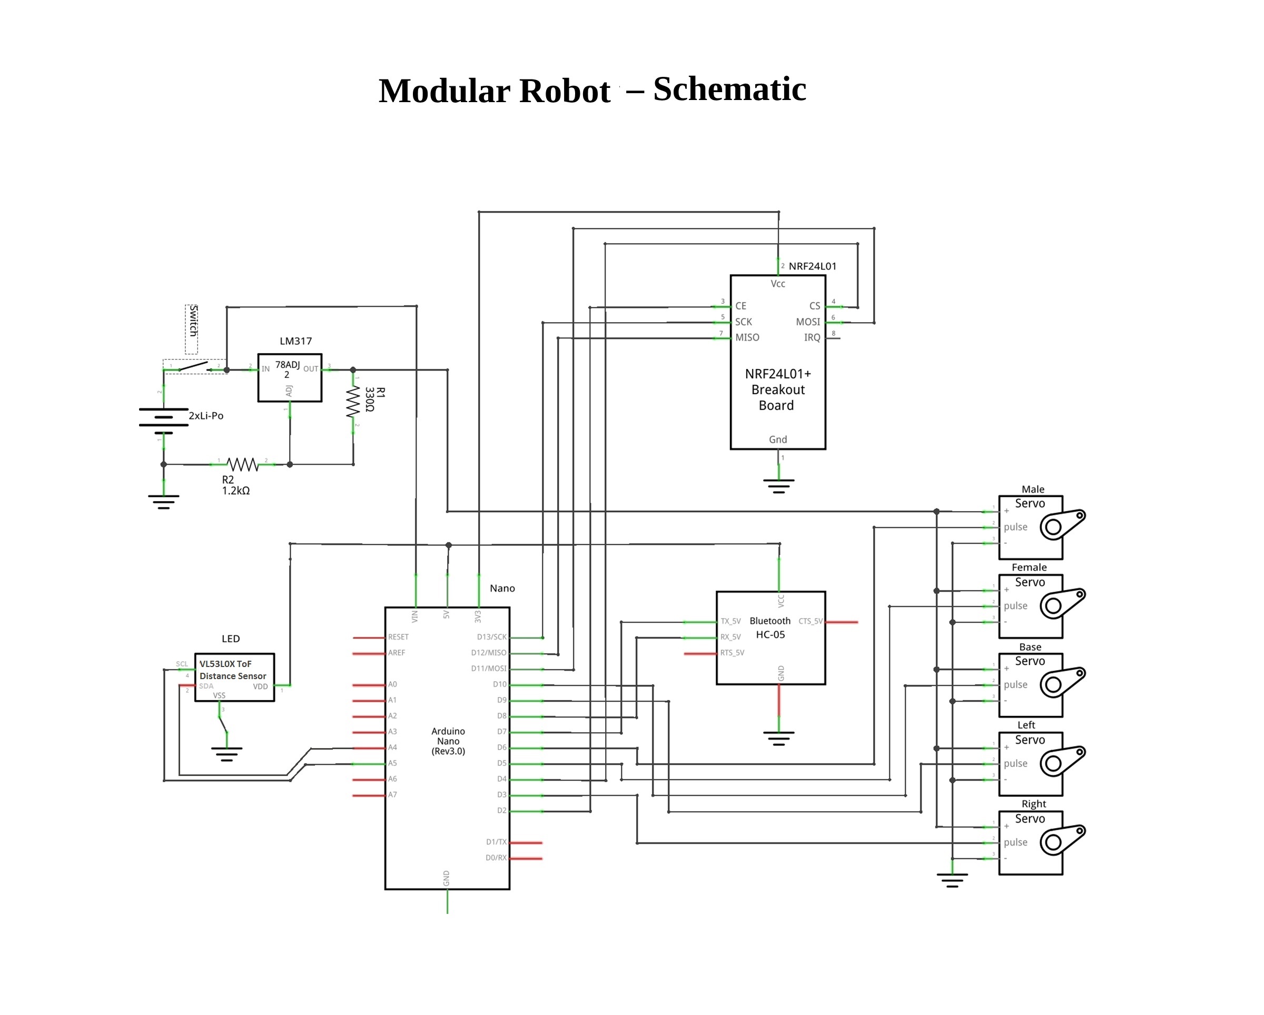
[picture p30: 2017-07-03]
Basic Interfacing/Schematics/Modular_Schematic.jpg

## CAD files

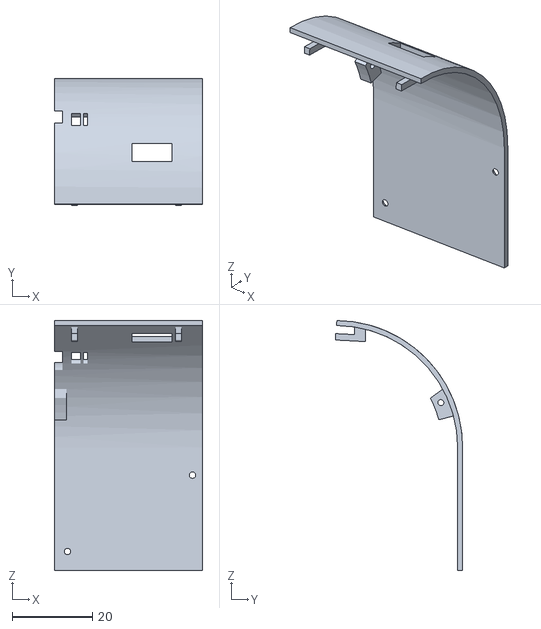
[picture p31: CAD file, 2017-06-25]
3D Files/1.6mm_screws_stl/001-1.stl
37.0 x 31.8 x 62.5

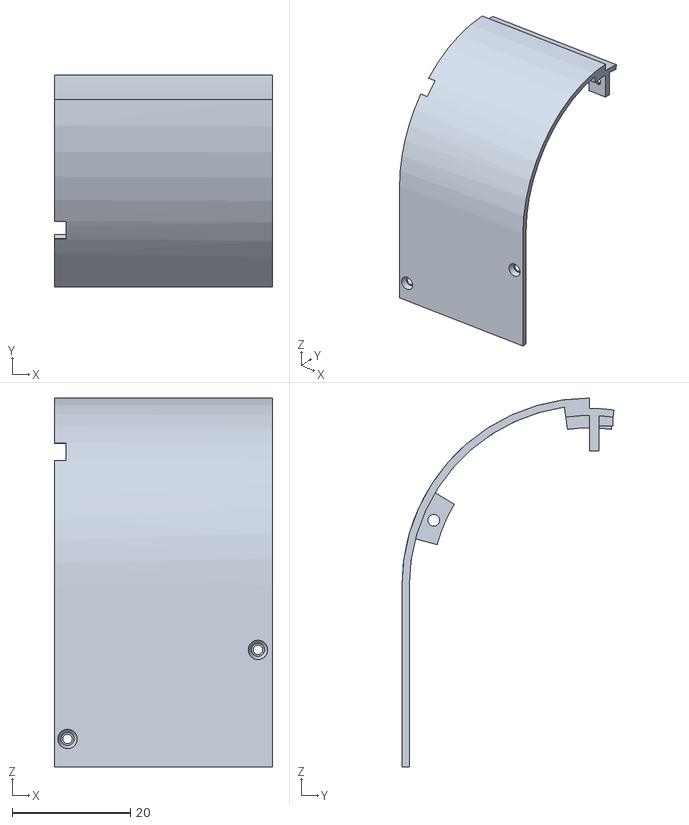
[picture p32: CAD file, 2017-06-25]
3D Files/2mm_screws_stl/002-1.stl
37.0 x 35.9 x 62.5

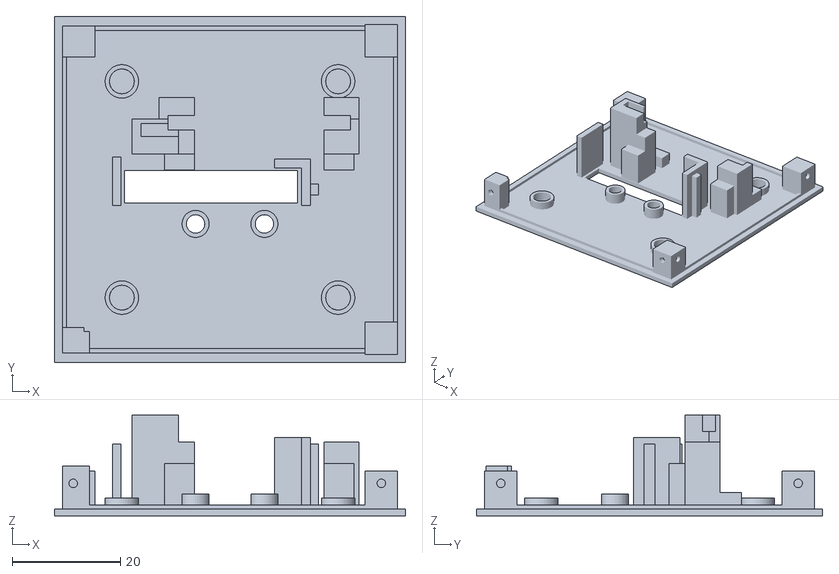
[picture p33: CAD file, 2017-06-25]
3D Files/1.6mm_screws_stl/005-1.stl
65.0 x 64.0 x 18.6

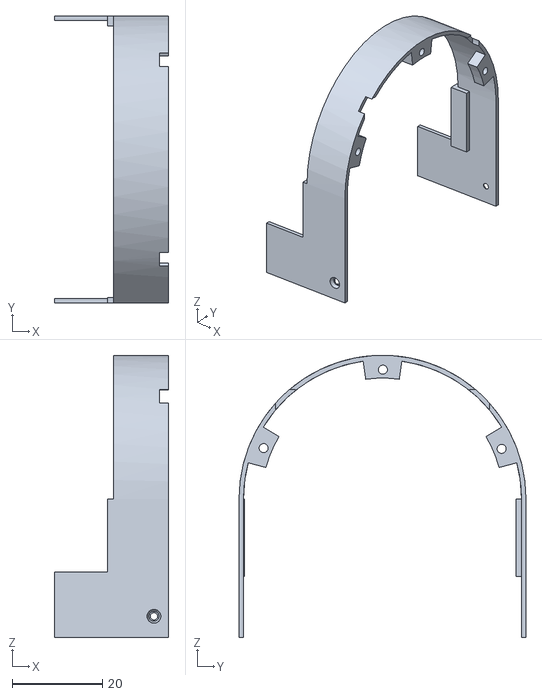
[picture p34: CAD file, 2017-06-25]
3D Files/2mm_screws_stl/003-1.stl
25.3 x 63.5 x 62.5

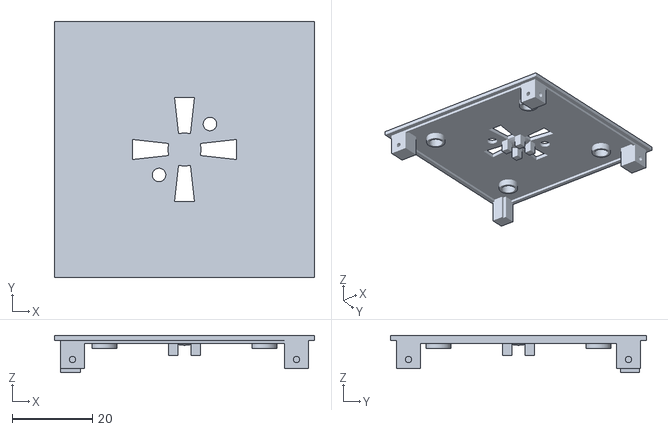
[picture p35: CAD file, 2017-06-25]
3D Files/1.6mm_screws_stl/006-1.stl
65.0 x 64.0 x 9.25

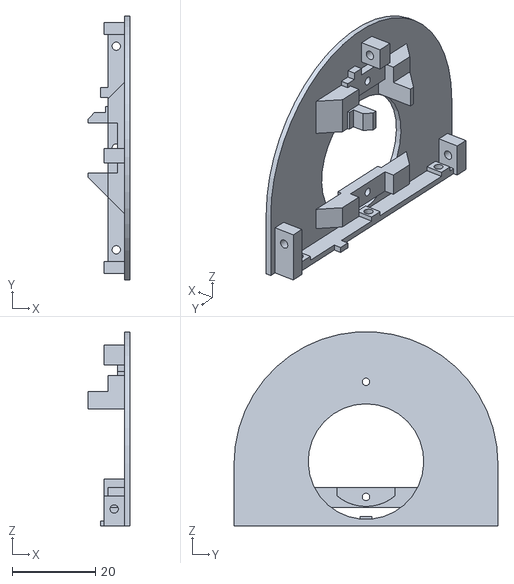
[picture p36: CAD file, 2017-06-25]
3D Files/2mm_screws_stl/004-1.stl
10.0 x 63.5 x 46.7

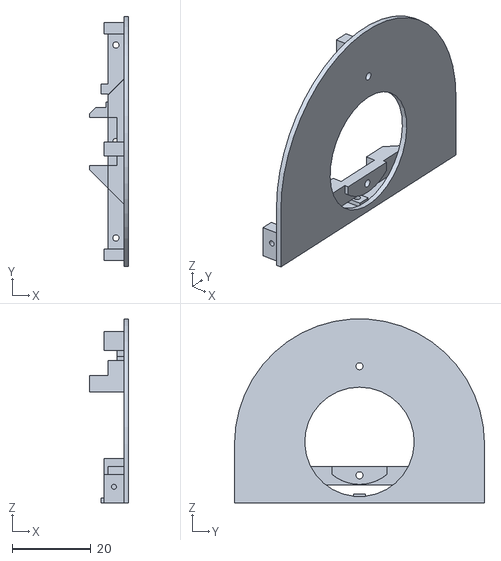
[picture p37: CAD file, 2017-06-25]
3D Files/1.6mm_screws_stl/004-1.stl
10.0 x 63.5 x 46.7

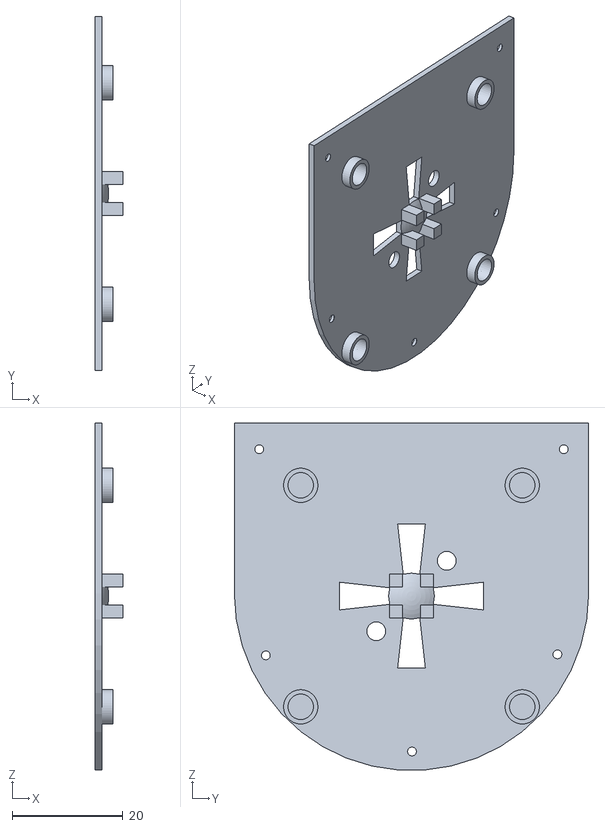
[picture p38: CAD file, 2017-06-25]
3D Files/2mm_screws_stl/008-1.stl
5.00 x 64.0 x 62.7

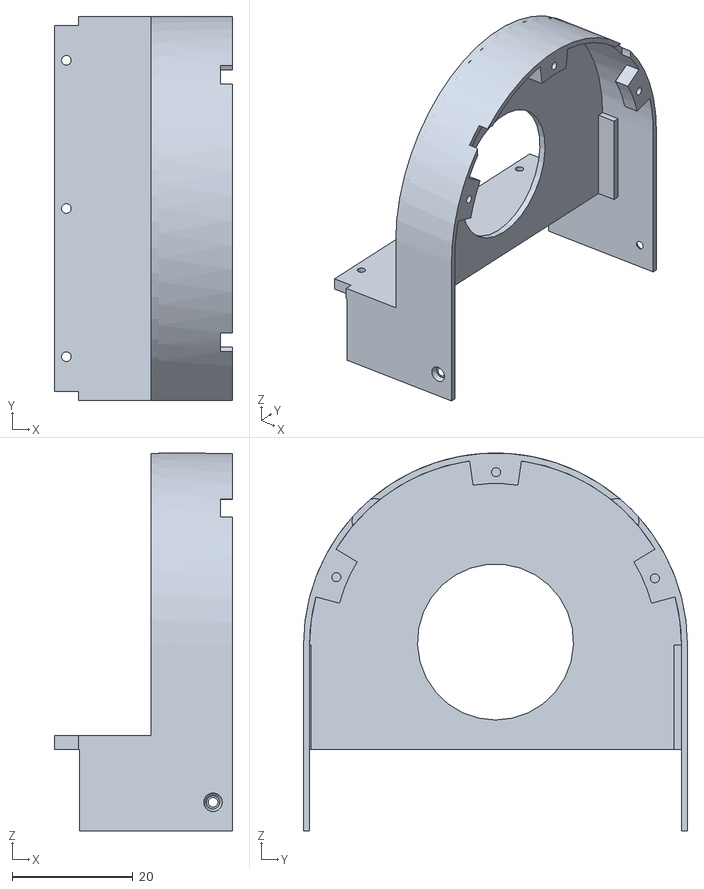
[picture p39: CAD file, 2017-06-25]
3D Files/1.6mm_screws_stl/003-2.stl
29.5 x 63.5 x 62.5

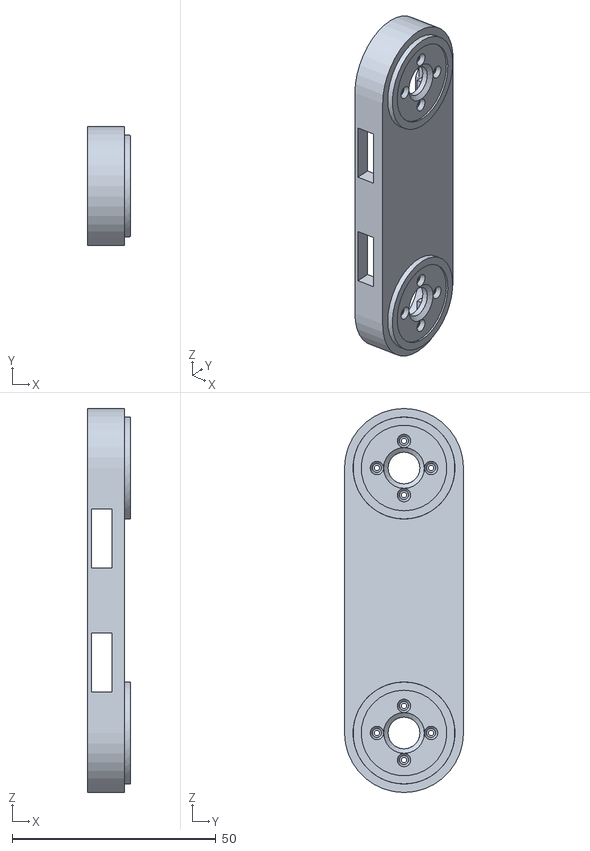
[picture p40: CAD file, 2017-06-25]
3D Files/2mm_screws_stl/012-1.stl
10.5 x 29.2 x 94.2

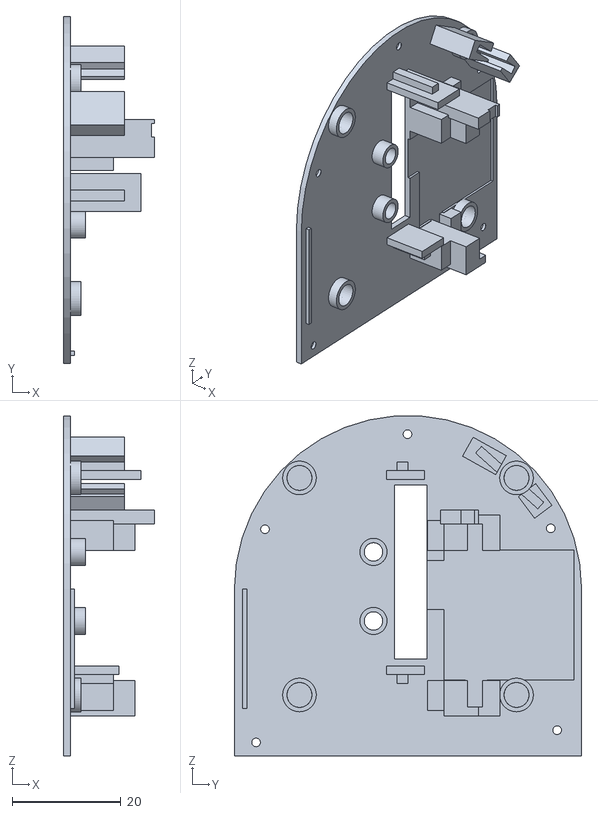
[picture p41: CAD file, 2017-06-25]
3D Files/2mm_screws_stl/007-1.stl
16.8 x 64.0 x 62.7

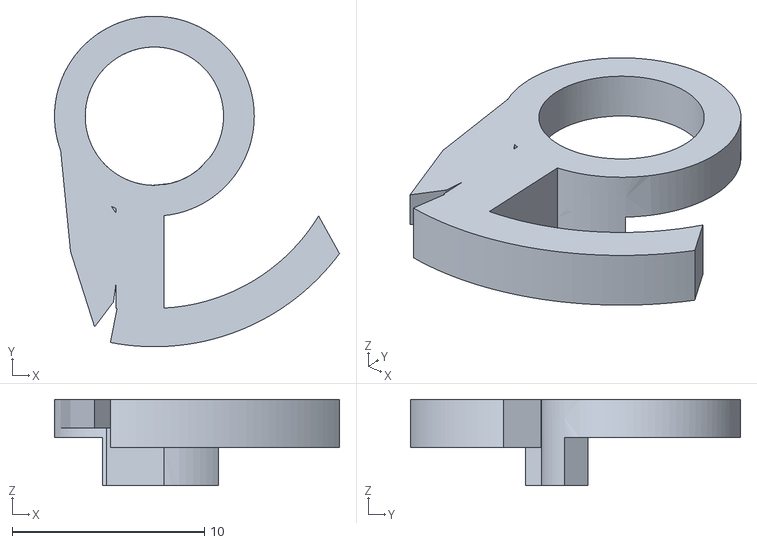
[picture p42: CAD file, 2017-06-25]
3D Files/2mm_screws_stl/014-1(ganchoB001).stl
14.8 x 17.2 x 4.50

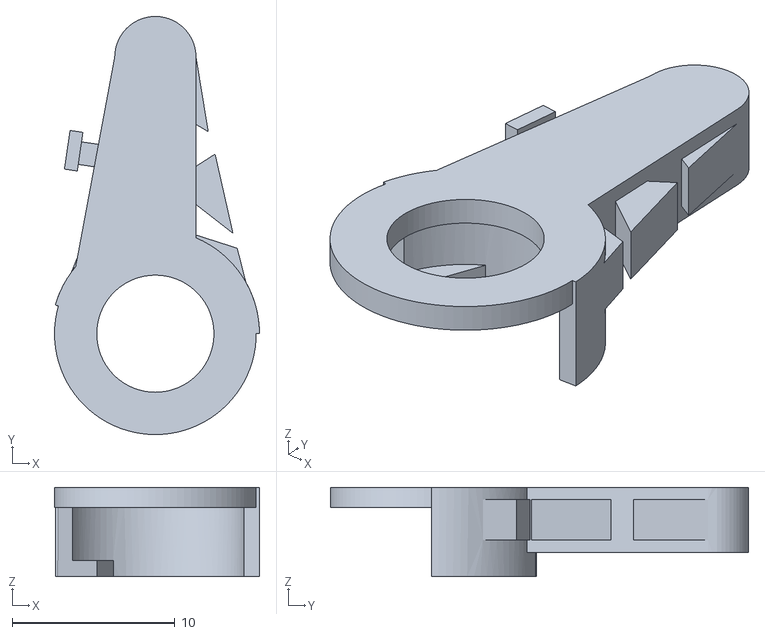
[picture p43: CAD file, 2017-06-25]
3D Files/2mm_screws_stl/013-1(ganchoA002).stl
12.6 x 25.7 x 5.50

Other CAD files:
3D Files/1.6mm_screws_stl/002-1.stl
3D Files/2mm_screws_stl/006-1.stl
3D Files/2mm_screws_stl/010-1.stl
3D Files/2mm_screws_stl/001-1.stl
3D Files/2mm_screws_stl/005-1.stl
3D Files/2mm_screws_stl/009-1.stl
3D Files/2mm_screws_stl/011-1(brazotapa002).stl

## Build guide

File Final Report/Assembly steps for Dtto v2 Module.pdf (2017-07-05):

# Assembly steps for Dtto v2 Module

Components required per module:

Quantity | Description
22 | 3D Printed Parts
1 | Arduino Nano v3.0
1 | HC-05 Bluetooth Module
1 | NRF24L01+ Wireless Transceiver
24 | Neodymium Disk Magnets (4x3mm)
2 | TowerPro MG90S Servomotor (MG92B recommended)
3 | TowerPro SG90 Servomotor
2 | Li-Po Battery 3.7V 500mAh
1 | LM317 Voltage Regulator
1 | Latching Switch for power
40 | M2x4mm countersunk screw
1 | 330 Ohms Resistor
1 | 1.2k Ohms Resistor
4 | 2.2k Ohms Resistor
3 | Small Rubber Band

### Final Schematic:

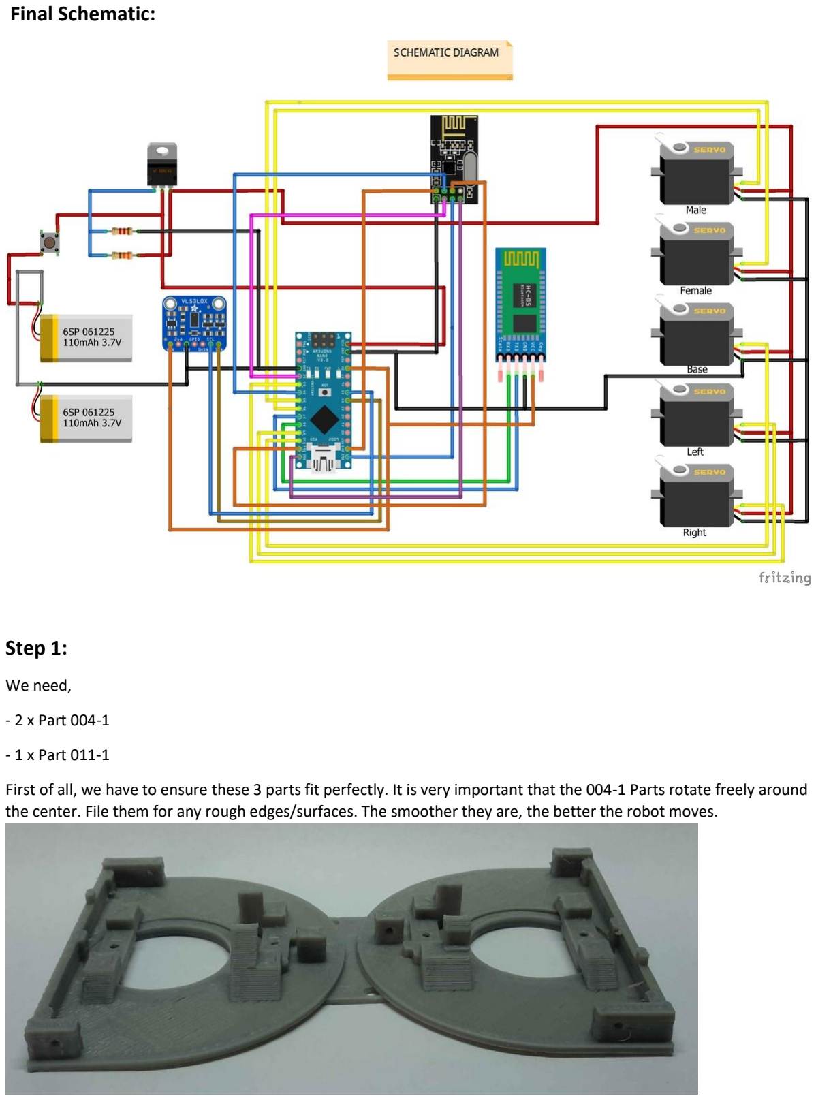
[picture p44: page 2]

### Step 1:

We need,

- 2 x Part 004-1
- 1 x Part 011-1

First of all, we have to ensure these 3 parts fit perfectly. It is very important that the 004-1 Parts rotate freely around the center. File them for any rough edges/surfaces. The smoother they are, the better the robot moves.

### Step 2:

For modifying the servos, we used 2.2k ohm resistors at both the potentiometer ends as shown in this video. (https://www.youtube.com/watch?v=ymW0Lwmw14Y) Also, we soldered thin 30 gauge wires inside the servo and brought it out to add resistors.

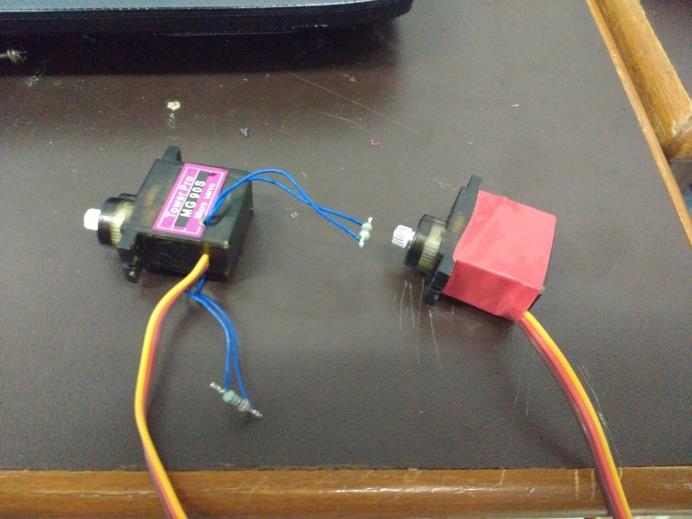
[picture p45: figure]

Directly adding the resistors inside was possible but involved a lot of hassle to fit it all back in the tiny case, so this was easier for us. After adding resistors, angles from 180 to 0 are between 140~130 to 22~28(vary slightly from motor to motor)

### Step 3:

We need,

- 2 x Part 004-1
- 2 x MG92B Servomotors (step 3)

In this step we are going to fix the motors to the printed parts. The motor should fit correctly. We can use the screws that come with the motor, but we will have to cut them to the right length.

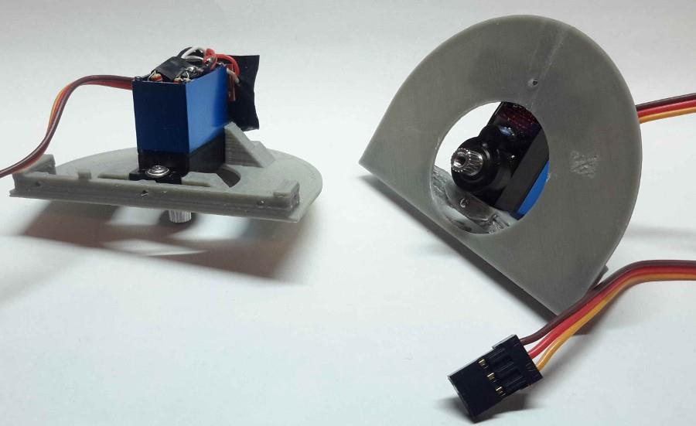
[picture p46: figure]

Upon screwing the servo to the hinge face, you will have to file the tip of the screw which comes out.

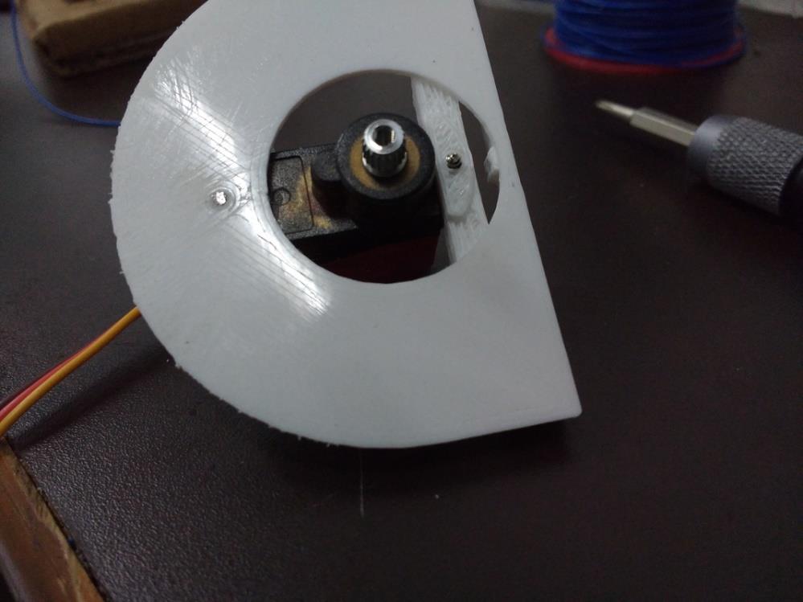
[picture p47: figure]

### Step 4:

We need,

- 1 x Part 011-1
- 1 x Part 012-1
- 2 x Servo Arm (Cross)

Now we are going to fix the servo arms to the 3D printed part. This step is very important because we have to ensure that the servomotor is centered. If it is not centered, once assembled, the module motor won’t be able to rotate all the way. The hinge must rotate from center to the sides at some angle in the range.

Once the servo worm is in a perfect position, it is helpful to use a hot soldering iron to just melt a tiny amount of servo worm with and into the hinge part so that it does not move when you screw the worm in.

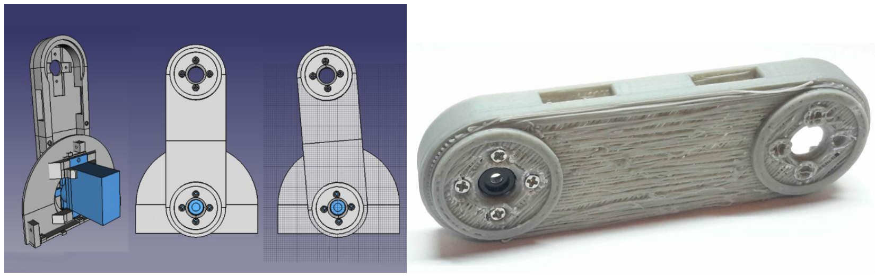
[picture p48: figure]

This is a critical part, so be sure to get a well centered configuration. Once we get a well centered part, we have to be completely sure that we got a correct configuration. Note down the center and side position angles somewhere as these would be entered later in the Dtto program.

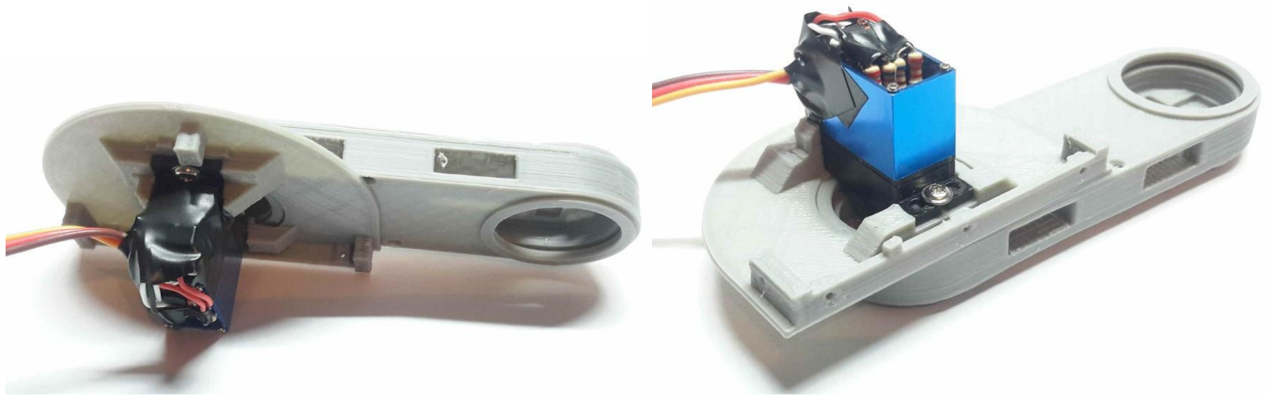
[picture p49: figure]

Once we finish with one servomotor, we can proceed to fix the other one.

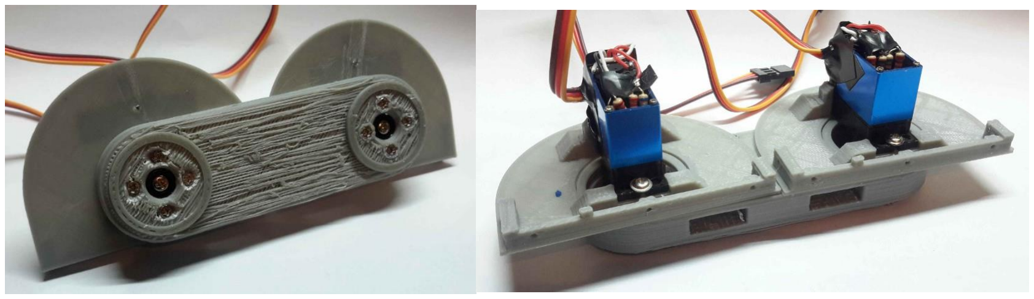
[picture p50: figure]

At this moment, the module does not have a male or female part assigned. We will choose one half and we will name it Male. The other will be the Female half. Then, we have to put the cables of the female motor through the hole in the central part, to the male part. You have to ensure that the cables allow a free rotation of the parts.

### Step 5:

We need,

- 1 x Part 003-1

Now we will start to assembly the male half of the module. First of all we have to ensure that the hole in the part 003-1 fits with the previously assembled part 012-1. Once sanded, we can attach the part 003-1 to the part 004-1 using 3 screws.

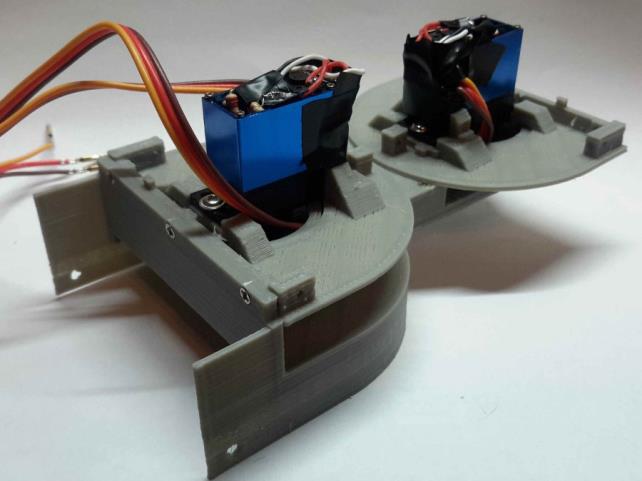
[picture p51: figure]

### Step 6:

We need,

- 1 x Part 005-1
- 1 x Part 007-1
- 1 x Part 009-1
- 12 x Neodymium Magnets

In this step we will put the magnets on the male parts. It is very important to put all the magnets in the male part with the north pole facing the inside of the module. We put the magnets in the holes, and then we put a drop of glue sticking it to the part. For this procedure, we like to use hot melt glue.

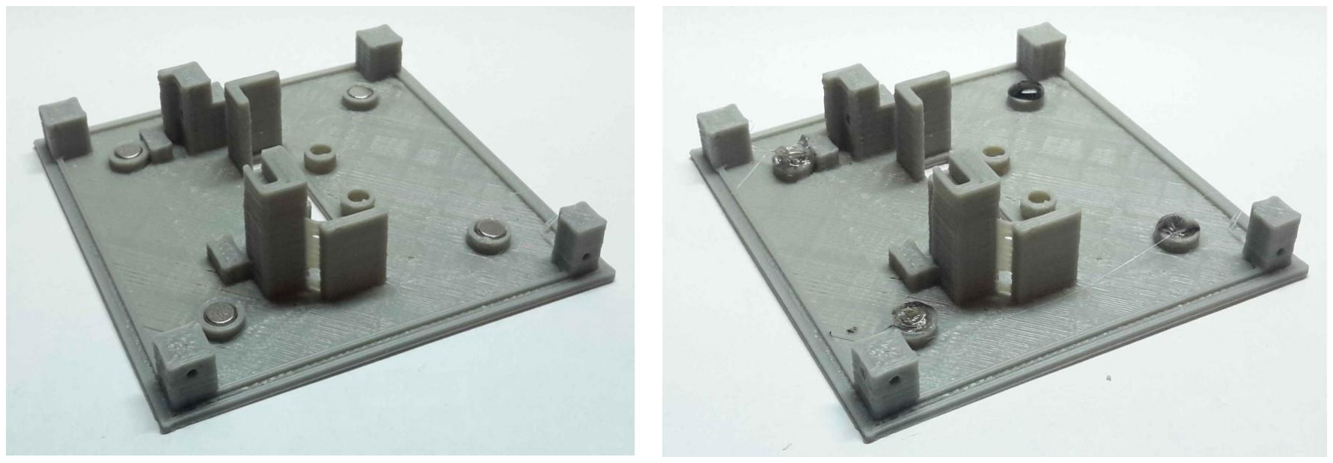
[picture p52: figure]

We repeat the procedure for the 3 parts.

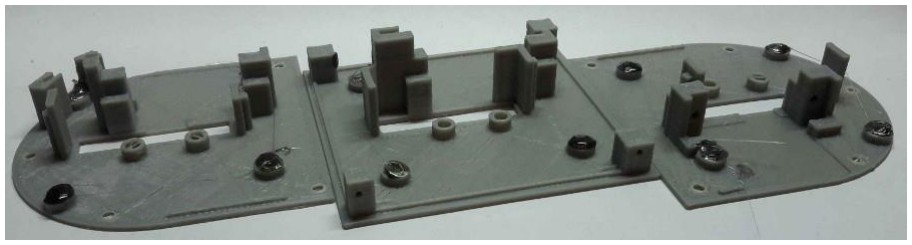
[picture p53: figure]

### Step 7:

We need,

- 1 x Part 006-1
- 1 x Part 008-1
- 1 x Part 010-1
- 12 x Neodymium Magnets

As we did in the previous step, we will put the magnets in the female parts. Now, remember to put all magnets with the north pole facing the outside of the module. If we do this correctly, the male parts won’t stick between them, but a male and a female part will be magnetically attracted.

### Step 8:

We need,

- 3 x SG90 Servomotors
- 3 x Part 013-1
- 3 x Part 014-1
- 3 x Small Rubber Band

In this step we will prepare the coupling mechanism that holds the modules of the robot together. We first insert the servo arm (cut as in the pic) through the two printed parts. We have to ensure that these parts rotate freely around the servo arm. We put the servo in the 90º position (servo.write(90)), and then we screw the parts like in the picture, using the screw that came with the servo. Finally, we put the rubber band between the two parts.

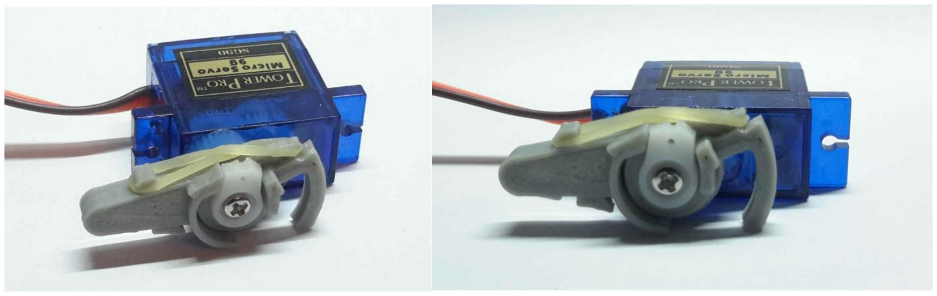
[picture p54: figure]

We repeat the procedure with the 2 SG90 servomotors left.

### Step 9:

We need,

- 1 x Part 005-1 (step 7)
- 1 x Part 007-1 (step 7)
- 1 x Part 009-1 (step 7)

In this step we will fix the servos that form the coupling mechanism to the printed parts. First we will insert the servo in the correct position. Then, using the 2 screws that came with the servo, we will fix it to the part.

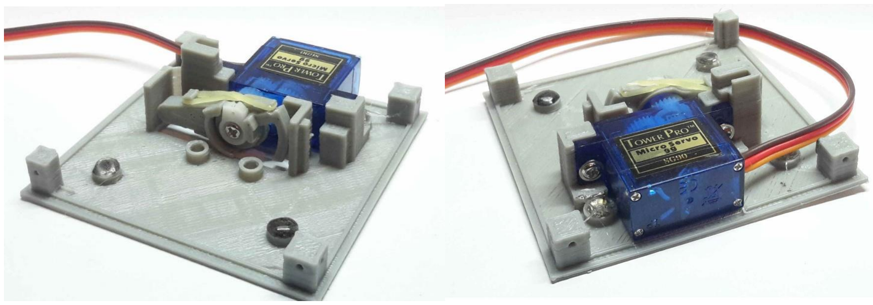
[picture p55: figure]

We will repeat the procedure for the 2 parts left.

### Step 10:

We need,

1 x HC-05 Bluetooth module

1 x NRF24L01 radio module

In this step we will prepare the Bluetooth and the radio module. We will have to remove the pin headers to solder wire directly, thus reducing the total volume of the modules. We used the thin 30 gauge insulated wires used for the servo modification again for wiring the HC-05 and nRF24 modules. It's thin and fits and bends easily inside the tightly packed modules.

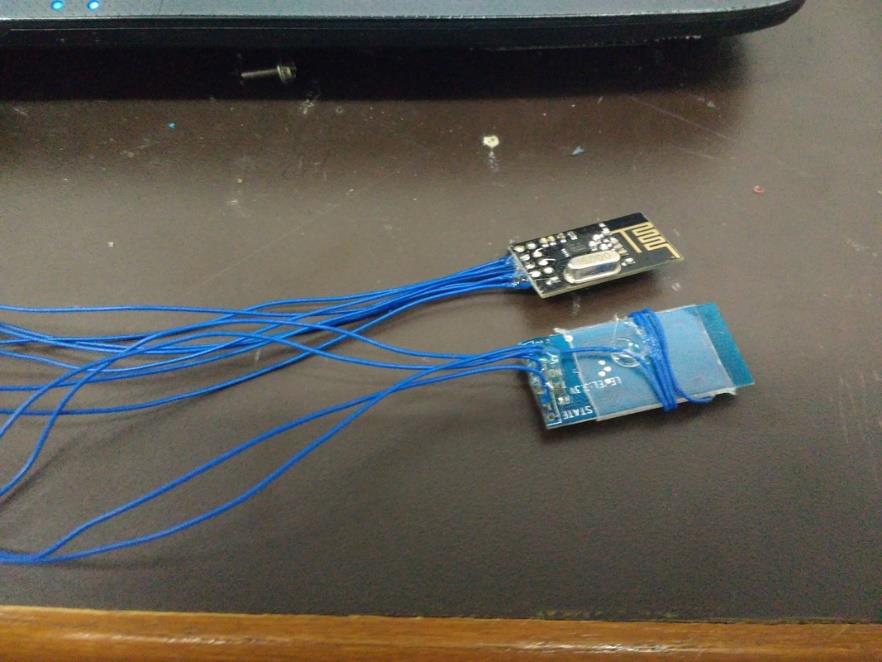
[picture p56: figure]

### Step 11:

We need,

- 1 x NRF24L02 radio module (step 11)

Now we are going to stick the radio module to its final position. Due to the lack of space and the need to reduce weight, we decided to simple stick the module with some hot melt glue. We have to be sure that the module doesn’t make contact with the moving part in the center. The cables go to the other side of the module.

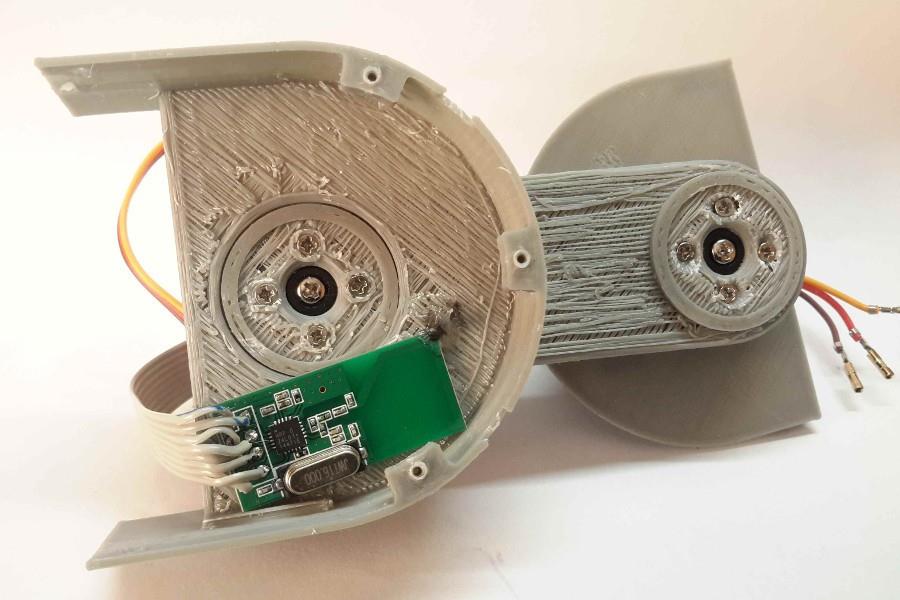
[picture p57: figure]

### Step 12:

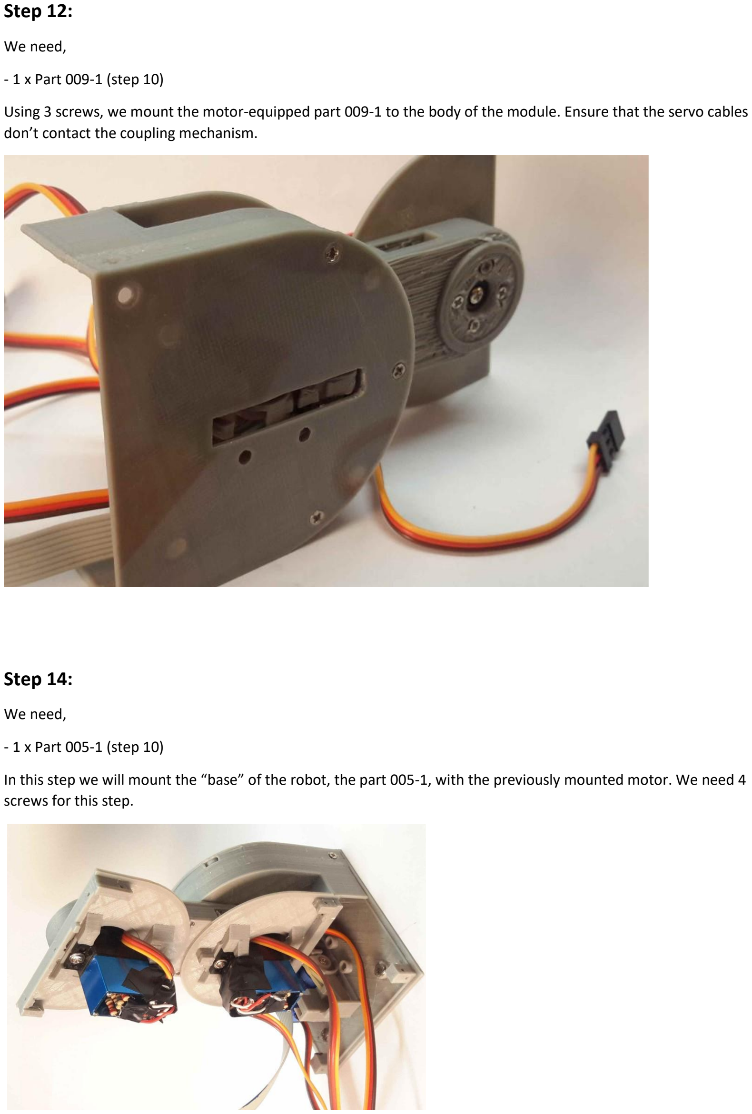
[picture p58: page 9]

We need,

- 1 x Part 009-1 (step 10)

Using 3 screws, we mount the motor-equipped part 009-1 to the body of the module. Ensure that the servo cables don’t contact the coupling mechanism.

### Step 14:

We need,

- 1 x Part 005-1 (step 10)

In this step we will mount the “base” of the robot, the part 005-1, with the previously mounted motor. We need 4 screws for this step.

### Step 15:

We need,

- 1 x LM317 Voltage Regulator
- 1 x 1200 Ohm Resistor
- 1 x 330 Ohm Resistor

Now we will configure our voltage regulator. Since we basically need the regulator for powering the servomotors, and since they can operate between 5 and 6 volts, we will set the regulator to the closer to 6 volts we can. We can use any other voltage regulator we want, considering the minimum current needs.

The LM317 Voltage regulator allows us to adjust the output voltage using some resistors. You can find the details and the math in its datasheet, widely available. Refer to the datasheet to be sure of the connections. The resistors that we choose were 330 and 1200 Ohms, resulting 5.8 volts. We can also use 100 and 390 Ohms, resulting in 6.1 volts. Check the schematics.

We need to power 5 servomotors with the output voltage from the regulator, so we need a small board to solder up the regulator, the resistors and the cables. The dimensions of the board shouldn’t exceed 1*2.2cm, and it should fit in the module as in the next pictures.

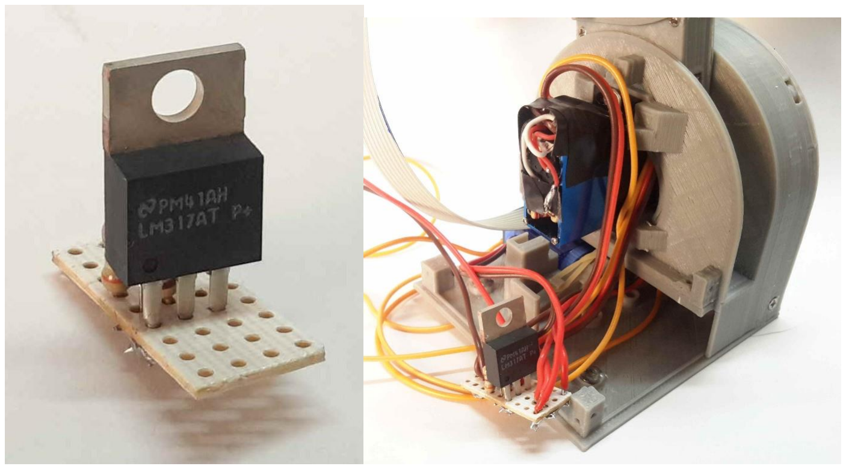
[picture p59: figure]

If we check the schematics of the module, we can see that we can use the board to connect the cables that come from the batteries (switch), and the ones that connect to the Arduino.

### Step 16:

Next, attach the female faces and base to the female half and leave one side open. Also solder the Radio and Bluetooth modules to the Arduino (Refer Schematics).

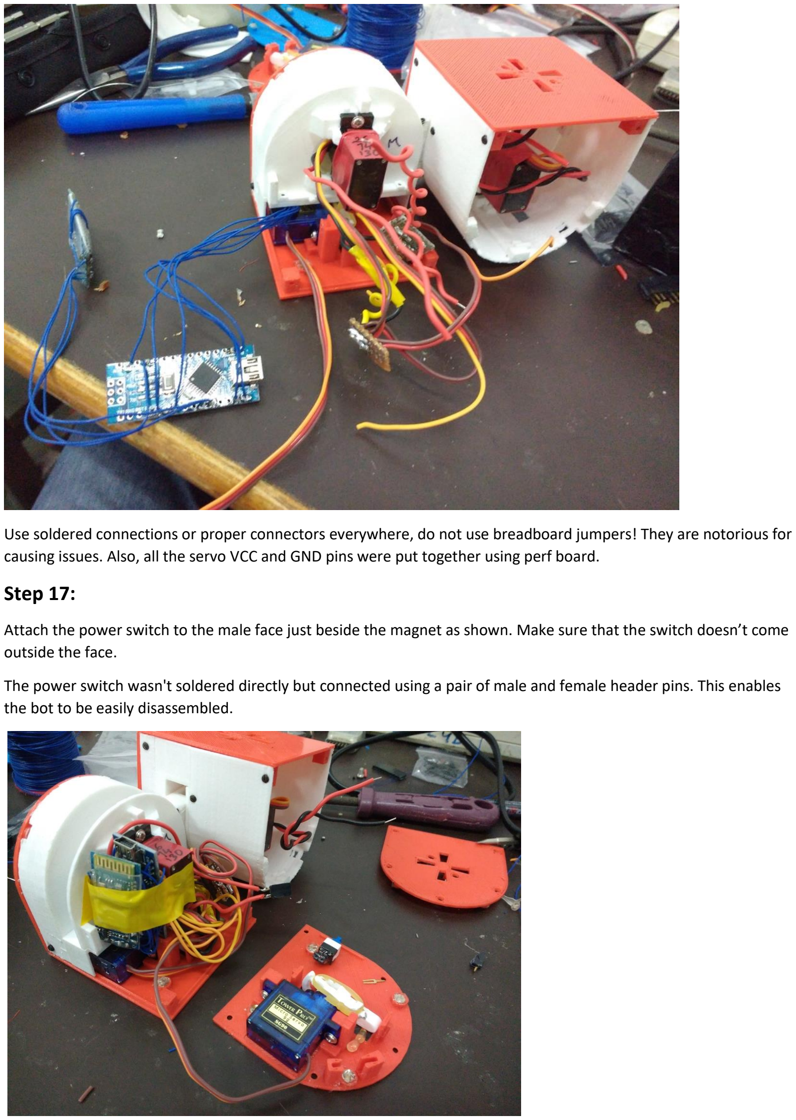
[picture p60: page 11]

Use soldered connections or proper connectors everywhere, do not use breadboard jumpers! They are notorious for causing issues. Also, all the servo VCC and GND pins were put together using perf board.

### Step 17:

Attach the power switch to the male face just beside the magnet as shown. Make sure that the switch doesn’t come outside the face.

The power switch wasn't soldered directly but connected using a pair of male and female header pins. This enables the bot to be easily disassembled.

### Step 18:

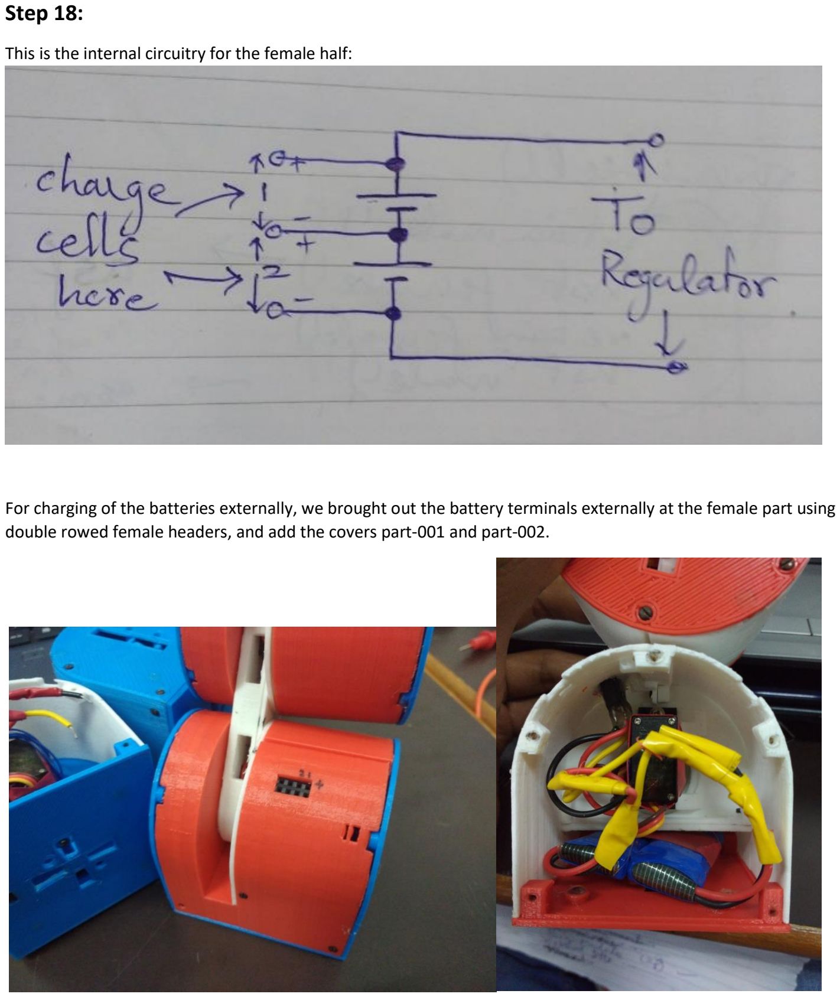
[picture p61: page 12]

This is the internal circuitry for the female half:

For charging of the batteries externally, we brought out the battery terminals externally at the female part using double rowed female headers, and add the covers part-001 and part-002.

### Step 19:

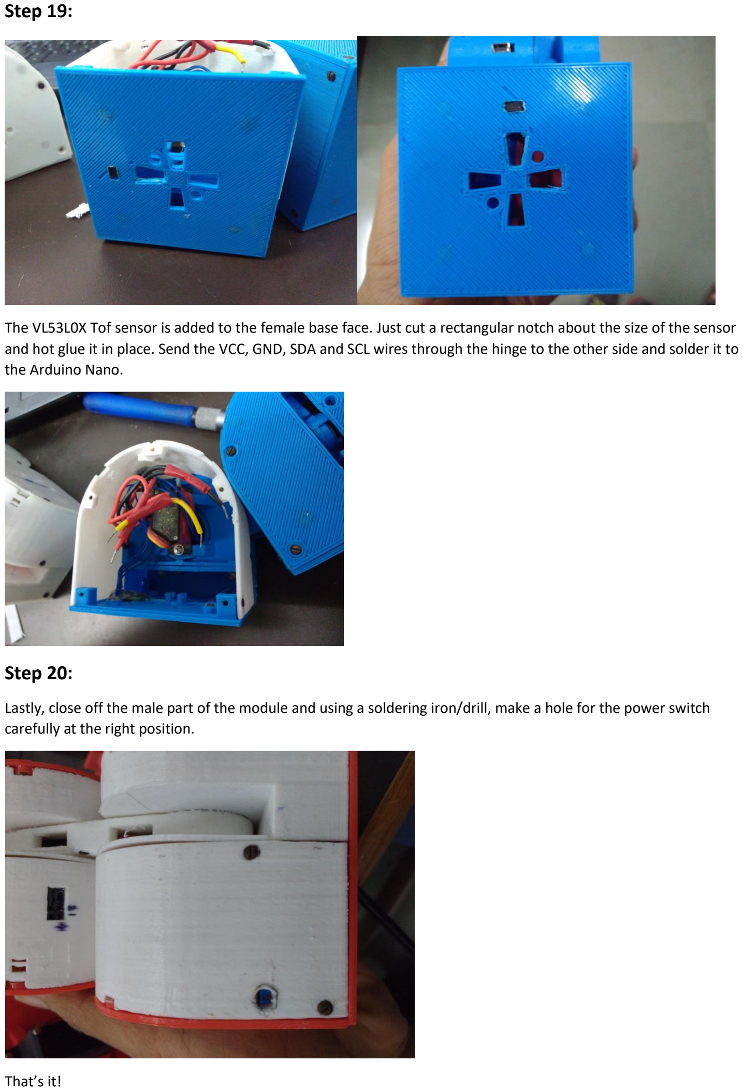
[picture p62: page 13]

The VL53L0X Tof sensor is added to the female base face. Just cut a rectangular notch about the size of the sensor and hot glue it in place. Send the VCC, GND, SDA and SCL wires through the hinge to the other side and solder it to the Arduino Nano.

### Step 20:

Lastly, close off the male part of the module and using a soldering iron/drill, make a hole for the power switch carefully at the right position.

That’s it!

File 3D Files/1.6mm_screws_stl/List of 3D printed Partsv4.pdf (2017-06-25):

### Dtto Modular Robot - 3D Printed Parts Needed (v2.0.1)

Here there is a listing of all the 3D parts needed for building a module. They are positioned the way we think it will be best for FDM printing.

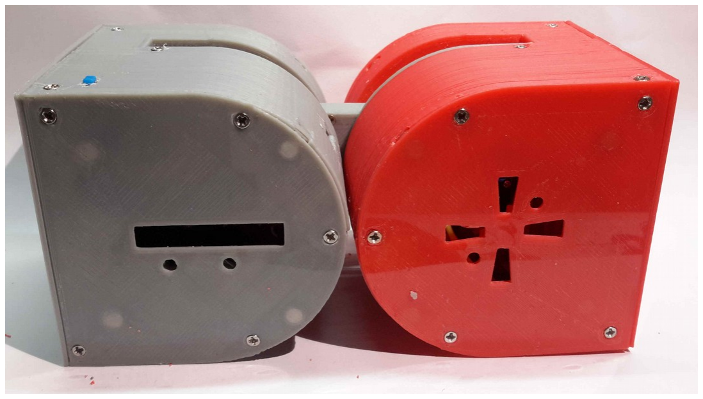
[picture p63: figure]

The module on the above picture was printed in two colours: A: Grey; B: Red.

The parts files are available for download at: https://github.com/otrebla333/Dtto-Modular-Robot Project:
https://hackaday.io/project/9976-dtto-v20-modular-robot

The parts were usually printed at 0.2mm layer height, 0.4mm nozzle size. Some parts require sanding in order to fit/slide properly.

QTY = Quantity
Part Nº | QTY | Color | Part Name | Position
001-1 | 2 | A & B | curvaext002.stl (support everywhere)

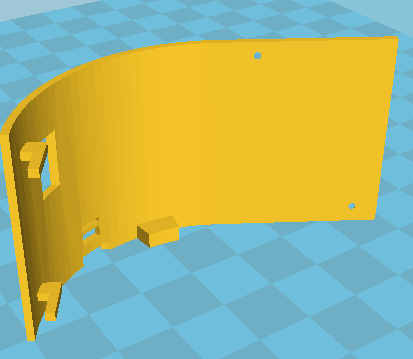
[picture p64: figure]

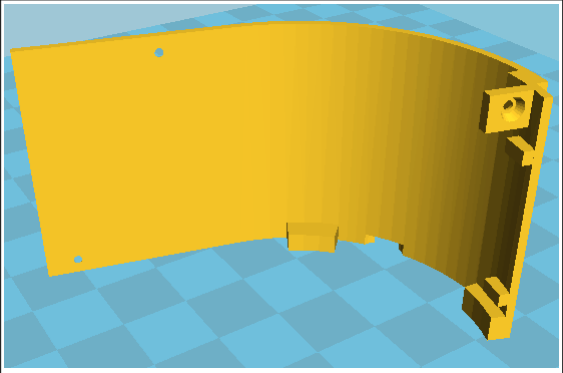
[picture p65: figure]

002-1 | 2 | A & B | curvafija002.stl (support everywhere)

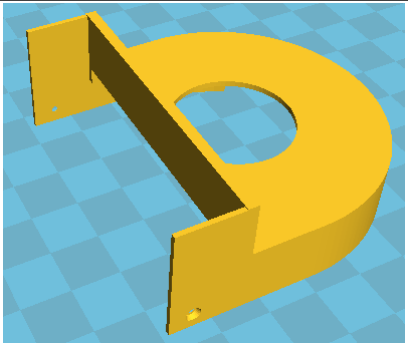
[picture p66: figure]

003-1 | 2 | A & B | paredcurva003. stl (support touching buildplate)

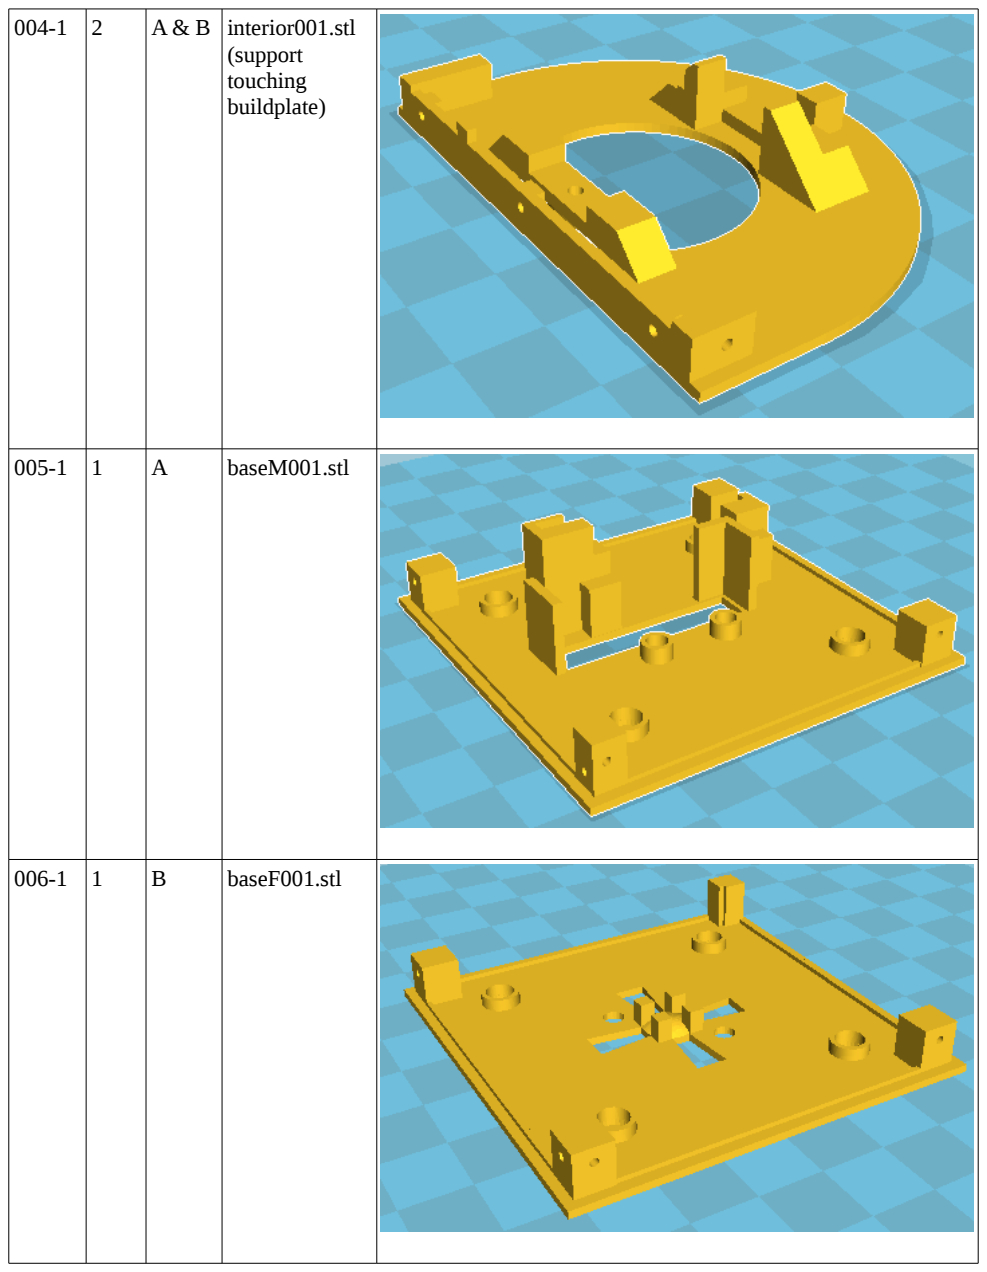
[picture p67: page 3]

004-1 | 2 | A & B | interior001.stl (support touching buildplate)
005-1 | 1 | A | baseM001.stl
006-1 | 1 | B | baseF001.stl

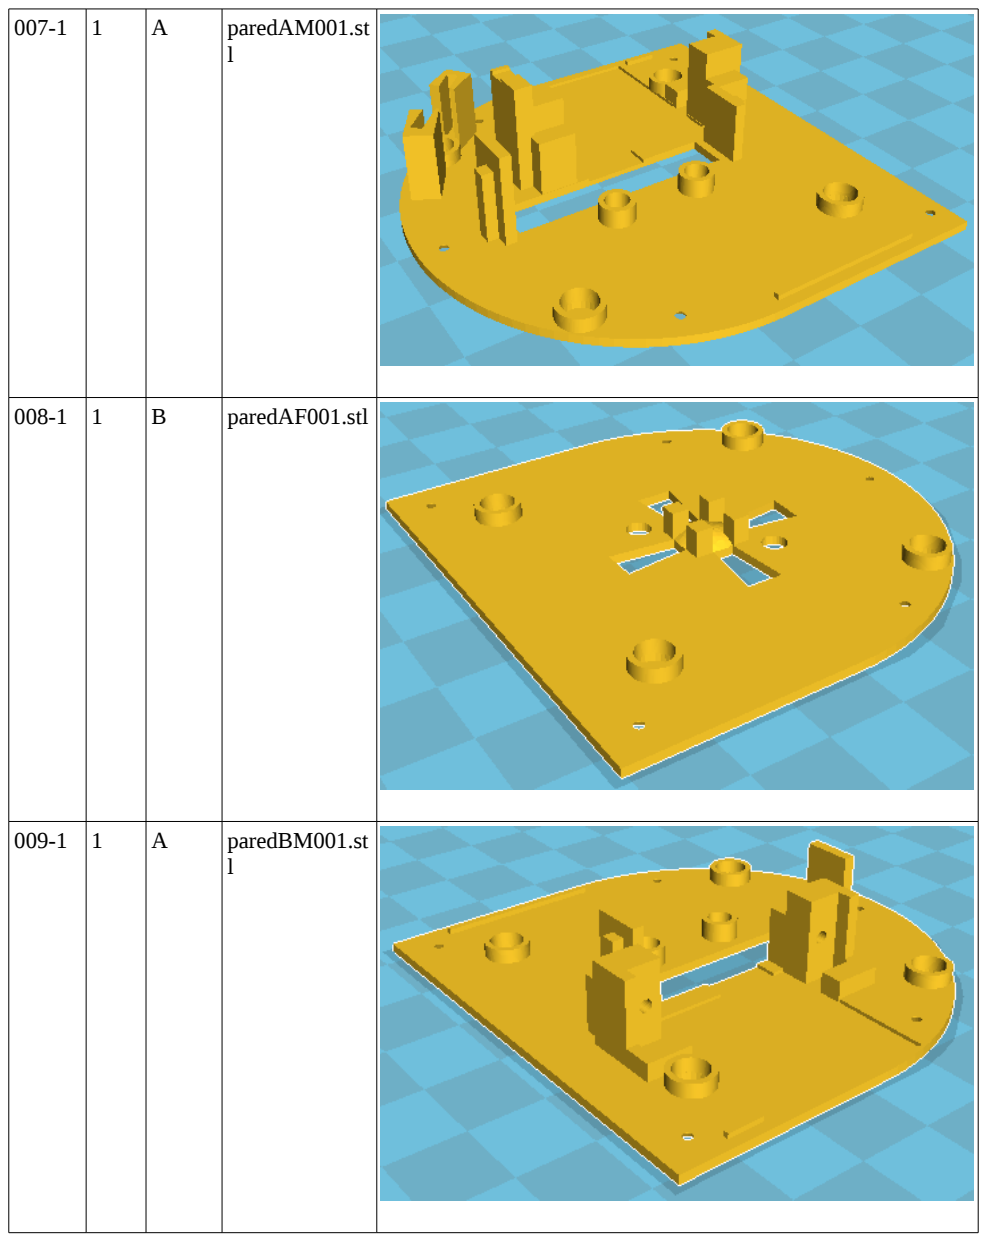
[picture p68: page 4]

007-1 | 1 | A | paredAM001.st l
008-1 | 1 | B | paredAF001.stl
009-1 | 1 | A | paredBM001.st l

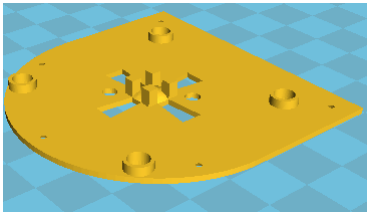
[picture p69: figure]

010-1 | 1 | B | paredBF001.stl

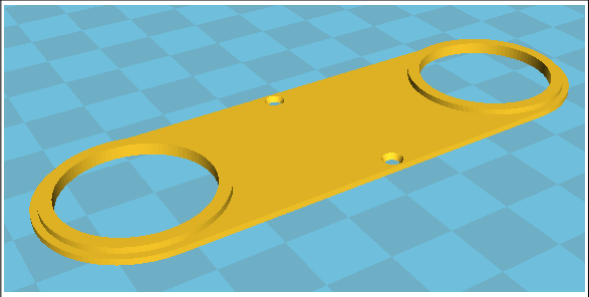
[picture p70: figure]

011-1 | 1 | A or B | brazotapa002.st l

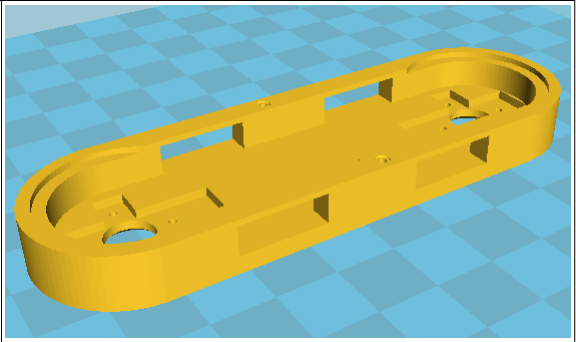
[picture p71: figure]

012-1 | 1 | A or B | brazobase002.s tl (support everywhere)

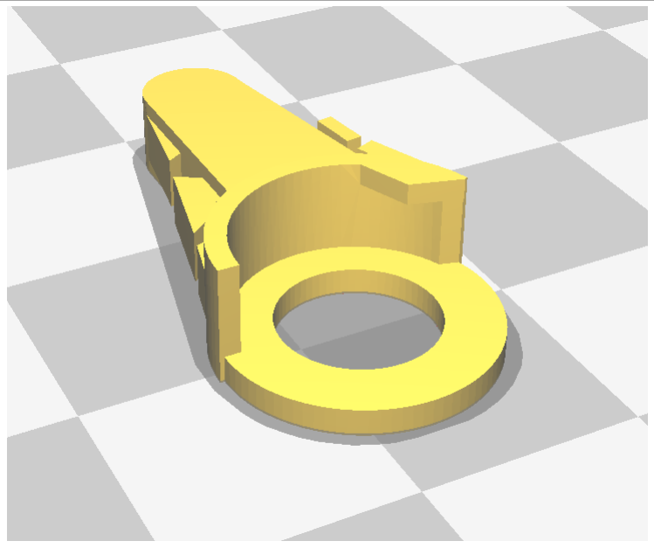
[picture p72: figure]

013-1 | 3 | A or B | ganchoA002.stl

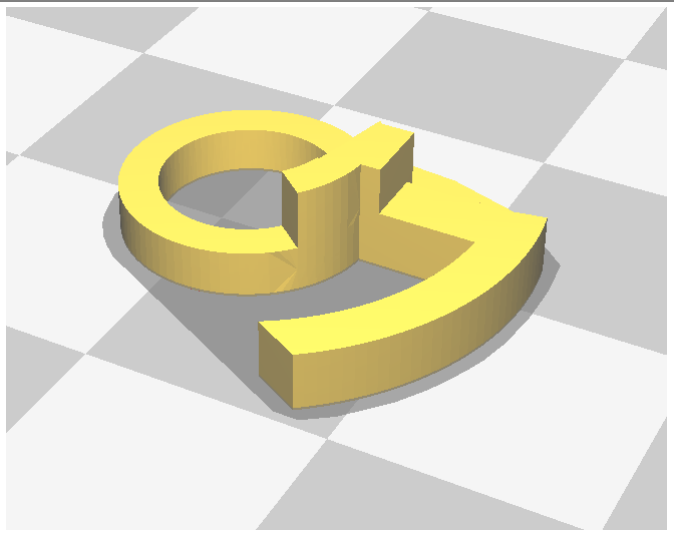
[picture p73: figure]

014-1 | 3 | A or B | ganchoB001.stl

This project and all of it's files, images and texts are entirely licensed under the CC BY-SA 4.0 license. (http://creativecommons.org/licenses/by-sa/4.0/legalcode)

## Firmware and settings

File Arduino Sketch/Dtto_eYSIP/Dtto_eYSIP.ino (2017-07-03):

/*
 * Authors: Srijal Poojari, Madhav Wagh
 * Description: Our program created for the Dtto modular robot for eYSIP 2017.
 * This standalone program includes code for both master and slave modules.
 *
 * Function List: setup(), loop(), get_module_num(), assign_module_num(),
 * listen_bluetooth(), listen_RF(), hook_attach(), snake(), set_angle(), escape(),
 * attach_servos(), detach_servos(), variation().
 */

#include <SoftwareSerial.h>
#include <Servo.h>
#include <SPI.h>
#include <nRF24L01.h>
#include <RF24.h>

#include <Wire.h>
#include <VL53L0X.h>

/*********************** Change before Upload *****************************/
#define DTTO_TYPE 1   //0 for MASTER module; 1 for the rest of SLAVE modules
int reverse = 1;      //used to negate angles in sinusoidal motion
#define HAS_SENSOR 0  //whether vl53l0x sensor is added or not
#define MODULE_BUILD_NUM 3 //physical id of the module. Used to define servo positions as
                           //each servo has different 'true physical angle' for angles written by servo.write()
                           //this is mainly because of modifications done to increase ranges by adding external resistances
/* example:
 * If angles in code go from: -90 ---  0 --- 90,
 * it actually translates to  130 --- 77 --- 26(example values).
 * i.e. to set 90 degrees on the servo, you actually have to write '26' because
 * of the modifications we did to increase servo range.
 */
/**************************************************************************/

#if HAS_SENSOR
VL53L0X tof_sensor;
#endif

#define CE_PIN 2   //RF24 Chip Enable pin
#define CSN_PIN 4  //RF24 Chip Select Not pin


//------------------------ Servo calibration -----------------------------//
//angles found out for each servo after modifications to increase range
int servo_center_positions_m[] = {74, 77, 80, 77};   //male center, 0 degrees
int servo_min_positions_m[] = {22, 26, 28, 26};      //min postition, 90 degrees
int servo_max_positions_m[] = {128, 133, 137, 133};  //max postition, -90 degrees

int servo_center_positions_f[] = {70, 74, 80, 74};   //male center, 0 degrees
int servo_min_positions_f[] = {20, 28, 28, 22};      //min postition, 90 degrees
int servo_max_positions_f[] = {128, 130, 137, 130};  //max postition, -90 degrees

#define SERVO_CENTER_M  servo_center_positions_m[MODULE_BUILD_NUM]    //Male hinge servo positions
#define SERVO_MIN_M  servo_min_positions_m[MODULE_BUILD_NUM]
#define SERVO_MAX_M  servo_max_positions_m[MODULE_BUILD_NUM]

#define SERVO_CENTER_F  servo_center_positions_f[MODULE_BUILD_NUM]     //Female hinge servo positions
#define SERVO_MIN_F  servo_min_positions_f[MODULE_BUILD_NUM]
#define SERVO_MAX_F  servo_max_positions_f[MODULE_BUILD_NUM]

//Servo hook positions, change as per your servo
#define SERVO_CENTER_HOOK 90  //neutral position
#define SERVO_MIN_HOOK 0      //hooked postion
#define SERVO_MAX_HOOK 150    //detach hook
//-----------------------------------------------------------------------//

//arrays to store mapped angles from software angle: -90---0---90 to the physical angles
//Values are mapped and stored beforehand as mapping it everytime when required is slower.
int mapped_angles_m[181];
int mapped_angles_f[181];

//variables for sinusoidal control
float speed_factor = 0.002; //Speed factor
int amp_factor = 40;      //Amplitude factor (basically max angle from center position to either sides)
unsigned long t = 0;      //Time auxiliary variables for time varying sine wave
unsigned long t_start = 0;


byte reset = 1;   //used to indicate starting point(in time) for sine wave

//bluetooth definitions
SoftwareSerial bluetooth(7, 8); //Creating software serial for bluetooth module (RX,TX)
String bt_rx_data;    //buffer for bluetooth received data

//RF24 definitions
RF24 radio(CE_PIN, CSN_PIN); //radio object for RF24 class
const uint64_t pipes[2] = { 0xE8E8F0F0E1LL, 0xF0F0F0F0D2LL };  //2 pipe addresses defined.
                                                               //1 for MASTER->SLAVES, 2 for SLAVES->MASTER
char rf_tx_data[8];   //buffers for transmit and receive data
char rf_rx_data[8];

String final_rx_data; //Final Received Data buffer which holds the command received, common for master as well as slave
                      //This is used to decide various actions performed in the main loop

int my_num = 1;   //Id of the module
int total_module_num = 1;    //Total number of modules

//Create servo objects
Servo servo_male;
Servo servo_female;
Servo servo_base;
Servo servo_right;
Servo servo_left;
//Note: 'Left' and 'Right' is defined with the Arduino USB port facing upward
//and male module is forward when viewed from the top as the reference.

//Angle variables used to set servo angles. Default values are defined below.
int servo_angle_male = 77;
int servo_angle_female = 77;
int servo_angle_base = 90;
int servo_angle_right = 90;
int servo_angle_left = 90;

bool stop_flag = false;    //Flag raised by sensor detection to indicate obstacle

int wheel_run_count = 0;   //number of times the run_wheel() function is run.
                           //Used to switch betwwen the wheel stages.
                           
char sign;   //Sign of angle retrieved from commands

void setup() {
  Serial.begin(9600);
  delay(1000);

  radio.begin();

#if DTTO_TYPE                           //If SLAVE,
  radio.openWritingPipe(pipes[1]);    //define channels
  radio.openReadingPipe(1, pipes[0]);
  get_module_num();                   //get id, stored in my_num

#else                                   //If MASTER.
  bluetooth.begin(9600);
  bluetooth.println("Reset");

  radio.openWritingPipe(pipes[0]);    //define channels
  radio.openReadingPipe(1, pipes[1]);
  radio.startListening();             //and start listening
#endif

#if HAS_SENSOR
  Wire.begin();

  tof_sensor.init();
  tof_sensor.setTimeout(500);

  // reduce timing budget to 20 ms (default is about 33 ms)
  // greater the budget, higher the accuracy but takes more time.
  tof_sensor.setMeasurementTimingBudget(20000);
#endif

  //map all software angles to true physical angles and store them.
  //this saves the calculation time when software angles are written
  for(int angle = -90; angle <= 0; angle++){   
    mapped_angles_m[angle + 90] = map(angle, -90, 0, SERVO_MAX_M, SERVO_CENTER_M);
    //angles go from -90 to 90, and array index goes from 0 to 180,i.e. angle+90
    mapped_angles_f[angle + 90] = map(angle, -90, 0, SERVO_MAX_F, SERVO_CENTER_F);
  }

  for(int angle = 1; angle <= 90; angle++){
    mapped_angles_m[angle + 90] = map(angle, 0, 90, SERVO_CENTER_M, SERVO_MIN_M);
    mapped_angles_f[angle + 90] = map(angle, 0, 90, SERVO_CENTER_F, SERVO_MIN_F);
  }

}

void loop() {
#if DTTO_TYPE       //If slave,
  listen_RF();    //listen for commands from master module via radio
#else                       //If master,
  assign_module_num();    //check if new modules asking for id and assign number
  listen_bluetooth();     //listen for commands
#endif

  switch (final_rx_data[1]) {    //Various blocks run based on commands in final_rx_data
  bluetooth.println(final_rx_data);
  case 'r': //Run, sinusoidal control
  #if HAS_SENSOR
    if (!stop_flag) {    //If stop_flag not raised
      snake();
    }
    else {    //Else, bot stopped, check if obstacle has been cleared

      int distance = tof_sensor.readRangeSingleMillimeters() - 30;
        //bluetooth.print("Distance (mm): ");
        //bluetooth.println(distance);
        if (distance < 90) {    //IF closer than 90mm, obstacle still present, remain still
          stop_flag = true;
          detach_servos();

          radio.stopListening();
          radio.write("ae", 2);    //Also command all bots to stop
          radio.startListening();
        }
        else {    // obstacle cleared, continue motion.
          stop_flag = false;
          attach_servos();

          radio.stopListening();
          radio.write("arm", 3);   //command other modules to resume motion
          radio.startListening();
        }
      //delay(100);
    }
  #else    //If no sensor, normal motion.
    snake();
  #endif

    break;
  case 'e':  //End all movement
    escape();
    break;
  case 's':  //Set angle manually
    set_angle();
    break;
  case 'h':  //attach module(hook)
    hook_attach();
    break;

  case 'n':   //'NOT' angle. Basically switches angle between 2 states, either 0<->90 or 0<->-90
              //This will be clear once you understand the wheel motion, explained on github.
    sign = final_rx_data[3];
    int angle;

    if (sign == '-'){   //If '-' specified by user, angle is negative
       angle = final_rx_data.substring(4, 6).toInt();    //get angle parameter and convert to int.
       angle = -1 * angle;
    }
    else{
       angle = final_rx_data.substring(3, 5).toInt();    //get angle parameter and convert to int.
    }

    //angle = 90, not_male(90) switches between 0 and 90
    //angle = -90, not_male(-90) switches between 0 and -90

    switch (final_rx_data[2]){
       case 'm':   //male
         not_male(angle);
         break;
       case 'f':
         not_female(angle);
         break;

       default:
         break;
    }
    final_rx_data = "";  //do not repeat command

    break;

#if !DTTO_TYPE   //Command only for master module
  case 'w':  //wheel
     switch (final_rx_data[2]){
       case 'p':   //prepare wheel postion
         prepare_wheel();
         final_rx_data = "";  //do not repeat
         break;
       case 'r':  //run wheel
         run_wheel();
         break;
       default:
         break;
     }
     break;
#endif

  default:
    break;
  }
}

void get_module_num() {    //slave modules get module number from master module
  int pass = 1234;   //pass to confirm request for id number
  detach_servos();   //detach servos to avoid power fluctuations which can affect communication

  while (my_num == 1) {  //while id not received from master, i.e. my_num is still 1
    radio.stopListening();   //stop listening before writing request
    radio.write(&pass, sizeof(int));
    radio.startListening();  //listen for response

    //Wait 500ms for a response. RF24 communication usually takes place within microseconds.
    unsigned long started_waiting_at = millis();
    bool timeout = false;
    while (!radio.available() && !timeout) {
      //If no response and timeout disabled for >500ms, timeout occurred
      if (millis() - started_waiting_at > 500)
        timeout = true;
    }

    if (!timeout) {  //If no timeout, which means data received in RF24 buffer
      radio.read(&my_num, sizeof(int));   //read id number
    }
  }
}

void assign_module_num() {   //master assigns id number to slave modules
  if (radio.available()) { //If some data received,
    int got_pass;
    radio.read(&got_pass, sizeof(int));
    if (got_pass == 1234) {  //If received data is 1234, module is asking for number.
      total_module_num++;  //total connected modules counter
      bluetooth.println("Module total: " + String(total_module_num));

      radio.stopListening();    //stop listening and send id to slave module
      radio.write(&total_module_num, sizeof(int));
      radio.startListening();

    }
  }
}

void listen_bluetooth() {    //listens commands from user via bluetooth

  if (bluetooth.available() > 0) {
    detach_servos();    //detach servos to avoid power fluctuations which can affect communication
    bt_rx_data = bluetooth.readStringUntil('\0');    //read data from buffer as a string
    bluetooth.println("Received: " + bt_rx_data);

    if (bt_rx_data[0] == '1') {         //first character '1' means command is just for master
      final_rx_data = bt_rx_data;
    }
    else if (bt_rx_data[0] == 'a') {  //'a' means command for master as well as all slaves
      final_rx_data = bt_rx_data;

      bt_rx_data.toCharArray(rf_tx_data, 8);   //convert received bluetooth command(String) to
                                         //char array for rf transmission
      radio.stopListening();
      radio.write(rf_tx_data, 8);
      radio.startListening();
    }
    else {                            //command just for slave modules
      bt_rx_data.toCharArray(rf_tx_data, 8);    //convert received bluetooth command(String) to
                                                      //char array for rf transmission
      radio.stopListening();
      radio.write(rf_tx_data, 8);
      radio.startListening();
    }
  }
}

void listen_RF() {
  if (radio.available()) {
    detach_servos();    //detach servos to avoid power fluctuations which can affect communication
    while (radio.available()) {
      //fetch the data payload
      radio.read(rf_rx_data, 8);
    }
    if ((rf_rx_data[0] == (my_num + 48)) || (rf_rx_data[0] == 'a')) {
      //If command is for me particularly or for all modules.
      //(my_num + 48) converts int to ASCII equivalent for char comparison

      final_rx_data = String(rf_rx_data);
    }
  }
}

void hook_attach() {
  switch (final_rx_data[2]) {
  case 'b':    //For base,
    servo_base.attach(10);
    if (final_rx_data[3] == '0')         //center position, usually enough for detaching
      servo_angle_base = SERVO_CENTER_HOOK;
    else if (final_rx_data[3] == '1')    //attach
      servo_angle_base = SERVO_MIN_HOOK;
    else if (final_rx_data[3] == '2')    //maximum detach
      servo_angle_base = SERVO_MAX_HOOK;

    servo_base.write(servo_angle_base);   // write the changed angle
    break;
  case 'r':    //For right sided servo,
    servo_right.attach(3);
    if (final_rx_data[3] == '0')
      servo_angle_right = SERVO_CENTER_HOOK;
    else if (final_rx_data[3] == '1')
      servo_angle_right = SERVO_MIN_HOOK;
    else if (final_rx_data[3] == '2')
      servo_angle_right = SERVO_MAX_HOOK;

    servo_right.write(servo_angle_right);
    break;
  case 'l':    //For left sided servo,
    servo_left.attach(9);
    if (final_rx_data[3] == '0')
      servo_angle_left = SERVO_CENTER_HOOK;
    else if (final_rx_data[3] == '1')
      servo_angle_left = SERVO_MIN_HOOK;
    else if (final_rx_data[3] == '2')
      servo_angle_left = SERVO_MAX_HOOK;

    servo_left.write(servo_angle_left);
    break;
  default:
    break;
  }
  delay(150);
  detach_servos();
}

void snake() {
  attach_servos();
  if (reset) {    //If first run of loop,
    t_start = millis();
  }
  t = millis() - t_start;
  reset = 0;

  //float angle_variation;    //difference between male and female angle values.

  switch (final_rx_data[2]) {

  case 'm':    //motion with male module facing front

    /* male_angle = amp_factor * sin(theta + phase + pi/2) = amp_factor * cos(theta + phase)
     * female_angle = amp_factor * sin(theta + phase)
     *
     * cos and sin is interchanged for reverse motion. This can be directly done using the 'reverse' variable(int).
     *
     * theta = time * speed_factor
     * phase = 180*module_nume ,i.e. it negates the sign of cos and sin for every alternate module,
     * since sin(a + pi) = -sin(a) and cos(a + pi) = -cos(a)
     *
     * amplitude factor scales the sin and cos values to degrees.
     */

    servo_angle_male = amp_factor * sin((speed_factor * t) + (my_num * PI)
                        + (1 - reverse) * PI / 2);
    servo_angle_female = amp_factor * sin((speed_factor * t) + (my_num * PI)
                        + (reverse * PI / 2));

#if HAS_SENSOR
    //angle_variation = variation(male_joint_angle, female_joint_angle);
    
    if (servo_angle_male < 0 && servo_angle_female > -2 && servo_angle_female <  2) {
     //condition for front face to face forward is that the half module containing the sensor(female)
     //has its hinge angle at the center(+2/-2) and the other half must be inclined upward.

      // bluetooth.println(servo_angle_male);
      // bluetooth.println(servo_angle_female);

      int distance = tof_sensor.readRangeSingleMillimeters() - 30;
      
//      bluetooth.print("Distance (mm): ");
//      bluetooth.println(distance);

      if (distance < 50) {    //If object closer than 50mm,
          stop_flag = true;    //raise stop flag
          //  bluetooth.println("Stop Flag=1");

          //restore hinges to center position
          modified_write(servo_male, 0, 0);
          modified_write(servo_female, 0, 1);

          radio.stopListening();
          radio.write("asm0", 4);
          delay(500);
          radio.write("asf0", 4);
          delay(500);
          radio.startListening();
       }
    }
#endif

    modified_write(servo_male, servo_angle_male, 0);
    modified_write(servo_female, servo_angle_female, 1);
    break;

  case 'f':    //motion with female module facing front
    servo_angle_male = amp_factor * sin((speed_factor * t) - (my_num * PI)
                                         + (1 - reverse) * PI / 2);
    servo_angle_female = amp_factor * sin((speed_factor * t) - ((my_num * PI)
                                         + reverse * PI / 2));

#if HAS_SENSOR
    //angle_variation = variation(male_joint_angle, female_joint_angle);

    if (servo_angle_male > 0 && servo_angle_female > -2 && servo_angle_female < 2) {
     //condition for front face to face forward is that the half module containing the sensor(female)
     //has its hinge angle at the center(+2/-2) and the other half must be inclined upward.

      // bluetooth.println(servo_angle_male);
      // bluetooth.println(servo_angle_female);

         int distance = tof_sensor.readRangeSingleMillimeters() - 30;
//         bluetooth.print("Distance (mm): ");
//         bluetooth.println(distance);

        if (distance < 50) {
          stop_flag = true;
          //  bluetooth.println("Stop Flag=1");

          //restore hinges to center position
          modified_write(servo_male, 0, 0);
          modified_write(servo_female, 0, 1);

          radio.stopListening();
          radio.write("asm0", 4);
          delay(500);
          radio.write("asf0", 4);
          delay(500);
          radio.startListening();
         
        }
    }
#endif

    modified_write(servo_male, servo_angle_male, 0);
    modified_write(servo_female, servo_angle_female, 1);

    break;
  default:
    break;
  }
  //detachServos();
}

void set_angle() {    //set a paricular angle to hinge servos
  //bluetooth.println(final_rx_data);

  //Two types of commands can be: 1sm90, 1sm-90
  //So for negative angles we must check for the '-' character
  sign = final_rx_data[3];
  int angle;

  if (sign == '-'){
    angle = final_rx_data.substring(4, 6).toInt();    //get angle parameter and convert to int.
    angle = -1 * angle;
  }
  else{
    angle = final_rx_data.substring(3, 5).toInt();    //get angle parameter and convert to int.
  }

  bluetooth.print("Angle: " + String(angle) + "\n\r");
  attach_servos();
  if ((angle <= 90) && (angle >= -90)) {    //If angle within range
    switch (final_rx_data[2]) {
    case 'm':    //for male hinge
      modified_write(servo_male, angle, 0);
      break;
    case 'f':    //for female hinge
      modified_write(servo_female, angle, 1);
      break;
    default:
      break;
    }
  }
  final_rx_data = "";
}

void escape() {    // stop all motion
  t = 0;
  detach_servos();
  reset = 1;
  wheel_run_count = 0;
}

void attach_servos() {    //attach servos to their pins
  servo_male.attach(6);
  servo_female.attach(5);
  servo_base.attach(10);
  servo_right.attach(3);
  servo_left.attach(9);
}

void detach_servos() {    //detach servos from thier pins
  servo_male.detach();
  servo_female.detach();
  servo_base.detach();
  servo_right.detach();
  servo_left.detach();
}

void modified_write(Servo &servo, int angle, int m_or_f){
  /* translates ideal physical angles from (-90,90) to angles required
   * by modified servos to set the required angle.
   * eg. -90 --- 0 --- 90 translates to 130 --- 77 --- 26
   * i.e. to set 90 degrees on the servo, you actually have to write '26' because
   * of the modifications we did to increase servo range.
   */

  if (m_or_f == 0){    //male
    int true_angle = mapped_angles_m[angle + 90];   //fetch angle from array
    //bluetooth.println(true_angle);
    servo.write(true_angle);
  }
  else if (m_or_f == 1){    //female
    int true_angle = mapped_angles_f[angle + 90];
    //bluetooth.println(true_angle);
    servo.write(true_angle);
  }
}

void prepare_wheel(){  //set the modules at their starting positions
  attach_servos();
  
  //straighten module 1: 0,0
  modified_write(servo_male, 0, 0);
  modified_write(servo_female, 0, 1);

  radio.stopListening();

  //module2: 90,-90
  radio.write("2sm90", 5);
  delay(1000);
  radio.write("2sf-90", 6);
  delay(1000);

  //straigthen module 3: 0,0
  radio.write("3sm0", 4);
  delay(1000);
  radio.write("3sf0", 4);
  delay(1000);

  //module 4: 90, -90
  radio.write("4sm90", 5);
  delay(1000);
  radio.write("4sf-90", 6);
  delay(1000);

  radio.startListening();
}

void run_wheel(){
  attach_servos();

  if(wheel_run_count % 2){   //retain male, NOT female
    radio.stopListening();
    radio.write("anf-90", 6);
    radio.startListening();

    not_female(-90);
  }
  else{    //retain female, NOT male
    radio.stopListening();
    radio.write("anm90", 5);
    radio.startListening();

    not_male(90);
  }
  delay(500);

  wheel_run_count++;
}
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

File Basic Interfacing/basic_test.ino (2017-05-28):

/* Program to test basic interfacing of Aruino with HC05 bluetooth modules,
 *  3x servo motors and a Sharp IR sensor.
 *  
 *  Date: 27/05/2017
 */

#include <Servo.h>
#include <SharpIR.h>

#define ir A0
#define model 1080
// ir: the pin where your sensor is attached
// model: an int that determines your sensor:  1080 for GP2Y0A21Y
//                                            20150 for GP2Y0A02Y
//                                            (working distance range according to the datasheets)

SharpIR SharpIR(ir, model);

//Create servo objects
Servo servo1;
Servo servo2;
Servo servo3;

String inputString = "";         // a string to hold incoming data
boolean stringComplete = false;  // whether the string is complete

int servo_num = 0;
int servo_pos = 0;
int prev_servo_pos = 0;  
int separator_idx = 0;    //Index of separator character ',' in inputString

//Range of servo numbers
int min_servo_num = 1;
int max_servo_num = 2;

//Range of servo values
int min_servo_pos = 0;
int max_servo_pos = 170;

int distance = 0;  //Distance in cm received from SharpIR.distance()

void setup(){
  // initialize serial:
  Serial.begin(9600);
  // reserve 200 bytes for the inputString:
  inputString.reserve(200);

  //initialize servos
  servo1.attach(7);
  servo2.attach(8);
  servo3.attach(9);
}

void loop(){
  if(stringComplete){ //when a newline char is received 
    //Serial.println(inputString);

    separator_idx = inputString.indexOf(',');
    if(separator_idx < 0){  //indexOf() returns -1 if char not present in string
      Serial.println("Invalid format! Enter as: servo_num,position ");
    }
    else{
       //get servo number and position as interger from inputString
       servo_num = inputString.substring(0, separator_idx).toInt();
       servo_pos = inputString.substring(separator_idx + 1).toInt();

       Serial.print("servo is: ");
       Serial.println(servo_num);
       
       Serial.print("position is: ");
       Serial.println(servo_pos);
       
       if((servo_num <= max_servo_num)and(servo_num >= min_servo_num)){
         //if servo number is in proper range then,
         if((servo_pos <= max_servo_pos)and(servo_pos >= min_servo_pos)){
           //if servo position is also in range then write values.
           if(servo_num == 1)
             servo1.write(servo_pos);
           if(servo_num == 2)
             servo2.write(servo_pos);
           if(servo_num == 3)
             servo3.write(servo_pos);
         }
         else{ //error in servo position
           Serial.print("Invalid servo position! Enter as servo_num,position. Possible values from ");
           Serial.print(min_servo_pos);
           Serial.print(" to ");
           Serial.println(max_servo_pos);
         }
       }
       else{ //error in servo number
         Serial.print("Invalid servo number! Enter as servo_num,position. Possible values from ");
         Serial.print(min_servo_num);
         Serial.print(" to ");
         Serial.println(max_servo_num);
       }
    }
    // clear the string:
       inputString = "";
       stringComplete = false; 
  }

  distance = SharpIR.distance();  //get distance

  //map the distance values ranging (8cm, 50cm) to servo position
  servo_pos = map(distance, 8, 50, min_servo_pos, max_servo_pos);

  if(servo_pos != prev_servo_pos){ //don't write same values again and again.
    
    if((servo_pos <= max_servo_pos)and(servo_pos >= min_servo_pos)){
       //if servo position is in range then write values.
       servo3.write(servo_pos);
     }
     prev_servo_pos = servo_pos;
  }
}

/*
  SerialEvent occurs whenever a new data comes in the
 hardware serial RX.  This routine is run between each
 time loop() runs, so using delay inside loop can delay
 response.  Multiple bytes of data may be available.
 */
void serialEvent(){
  while(Serial.available()){
    // get the new byte:
    char inChar = (char)Serial.read();
    // add it to the inputString:
    inputString += inChar;
    // if the incoming character is a newline, set a flag
    // so the main loop can do something about it:
    if(inChar == '\n'){
      stringComplete = true;
    }
  }
}

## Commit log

2017-05-26 Added Arduino Code
2017-05-27 Documentation Of Task-2
    Configured Bluetooth (Master & Slave), Interfaced Bluetooth Module, Arduino Nano, 3-Servo Motors, & Sharp Sensor & further checked their working
    [Config_Bluetooth_ATComm(Master Config).fzz, Config_Bluetooth_ATComm(Slave Config).fzz, Task2_Servo-3_Nano_HC05.fzz]
2017-05-28 Rearranged folder structure
    [Config_Bluetooth_ATComm(Master Config).fzz, Config_Bluetooth_ATComm(Slave Config).fzz, Task2_Servo-3_Nano_HC05.fzz]
2017-06-05 Combined slides, updated images
    [Task2_Servo-3_Nano_HC05.fzz]
2017-06-25 Added 3D CAD and STL files
    [001-1.stl, 002-1.stl, 003-1.stl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]
2017-06-26 Upload STL files for Mega Module
2017-06-26 Added Arduino sketch
2017-06-28 Added abstraction layer for angles before servo write
2017-07-03 Complete Interfacing Diagram
    [Modular_Schematic.fzz]
2017-07-04 Commands Description added
    Commands are used by user to run the modules.
    Referring to this document and simultaneously looking at the code also clears some basic code logic flow to the reader
2017-07-05 Update Flowchart
